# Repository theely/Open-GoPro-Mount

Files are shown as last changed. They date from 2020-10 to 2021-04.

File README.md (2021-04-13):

# Open GoPro Mount

A modular open source GoPro mount for FPV Drones.

## STL Files

[STL files](./STL) are ready to print GoPro Mounts, all available combinations of camera holders and frames mounts are available in the [STL folder](./STL)
If your specific camera model or frame is not yet supported, please [file a request](https://github.com/theely/Open-GoPro-Mount/issues).

### How to 3D Print

#### Filament

- The main body is designed to be printed with TPU (shore A95 or A98).
- The screen protector is best printed with rigid materials such as PLA, Nylon or hard TPU (shore D58)

#### Slicer Settings

- Infil Density: 30%
- Wall Lines: 4
- Top and Bottom Layers: 4
- Support: Yes

#### Slicer Optimal parts orientation




Note: This part can't be printed without support or the overhang will not print properly.

#### Printed Model Reference



## Design Principle

- Designed to be extremely duravble, ultra light and easy to 3D print.
- Modular approach to allow reusability of the component and easy portability to different quad frame designs.







## How to contribute?

The Open-GoPro-Mount is made of 4 components:

- Camera Holder
- Quad Frame Mount
- Lens protection
- Screen protection

### Porting the Open-GoPro-Mount to a new Quad Frame

To port the Open-GoPro-Mount to a new quad frame it's sufficent to design a new Quad Frame Mount.
Either by adapting an existing mount (e.g. Apex Mount (22.5°).step) or by design a new one from scratch.

The angle of the overal mount is defined by the Frame Mount, multiple mount angles can be supported by providing additional Quad Frame Mount featuring a set of angles.

#### Requirements

Each frame mount should include the following joint pice (red part) in order to be compatible with the Camera Holders.



The joint (red part) has the following dimensions:



Its important to respect the distance between the two red pieces:



### Adapting the Open-GoPro-Mount for a new Camera

To support additional cameras a new Cameras it's sufficent to desing a new Camera Holder.
Either by adapting an existing hodler (e.g. GoPro Hero 5/6/7 Holder.step) or by design a new one from scratch.

#### Requirements

Each camera holder should include the following joint holes in order to be compatible with the Quad Frame Mounts.



Distance between the holes are standardised and can not be changes.





The width of the holes does not necesarely be respected as long as there is enought material for the Quad Frame Mounts to join with the Camera Holder.



## Source File (Designs)

### Fusion360 Project

You can access the source design directly from the shared Fusion360

- [Fusion360 project](https://gmail784198.autodesk360.com/g/projects/20201018344143181/data/dXJuOmFkc2sud2lwcHJvZDpmcy5mb2xkZXI6Y28uZjc2MFRFNlhSaW1rVDFkaDE2NXdIdw)

### Step Files

Or you can import the shared step files and edit them in your favorite CAD program.

##### Cameras

- GoPro Hero 5/6/7
  - GoPro Hero 5/6/7 Holder.step
  - GoPro Hero 5/6/7 Holder Large.step (for wide frame mounts)
  - GoPro Hero 5/6/7 Lens Protection.step
  - GoPro Hero 8 Holder.step
  - GoPro Hero 8 Lens Protection.step

##### Frames

- Apex Support (22.5° and 15°).step
- DRC Flow Support (30°).step
- HyperLow 30x30 Mount (30°).step

##### Screen Protection

- GoPro Screen Protection.step

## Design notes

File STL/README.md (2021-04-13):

# STL Files

## How to 3D Print
### Filament
* The main body is designed to be printed with TPU (shore A95 or A98).
* The screen protector is best printed with rigid materials such as PLA, Nylon or hard TPU (shore D58)
### Slicer Settings
* Infil Density: 30%
* Wall Lines: 4
* Top and Bottom Layers: 4
* Support: Yes

### Slicer Optimal Parts Orientation




Note: This part can't be printed without support or the overhang will not print properly.

## Parts

### Screen Protections
* [GoPro Screen Protection.stl](./GoPro%20Screen%20Protection.stl)

### Frames

* Apex
  * [GoPro Hero 5/6/7 15°](./Apex%20-%20ImpulseRC/Apex%2015%C2%B0%20GoPro%20Hero%205-6-7%20Mount.stl)
  * [GoPro Hero 5/6/7 22.5°](./Apex%20-%20ImpulseRC/Apex%2022%C2%B0%20GoPro%20Hero%205:6:7%20Mount.stl)
  * [GoPro Hero 8 22.5°](./Apex%20-%20ImpulseRC/Apex%20GoPro%20Hero%208%20Mount%2022°.stl)
  
* Flow
  * [GoPro Hero 5/6/7 30°](./Flow%20-%20DemonRC/Flow%2030°%20GoPro%20Hero%205-6-7%20Mount.stl)

* Hyperlow
   *  [GoPro Hero 5/6/7 22.5°](./Hyperlow%20Frames/HyperLow%2030°%20GoPro%20Hero%205-6-7%20Mount.stl)
   *  [GoPro Hero 8 22.5°](./Hyperlow%20Frames/HyperLow%2030°%20GoPro%20Hero%208%20Mount.stl)

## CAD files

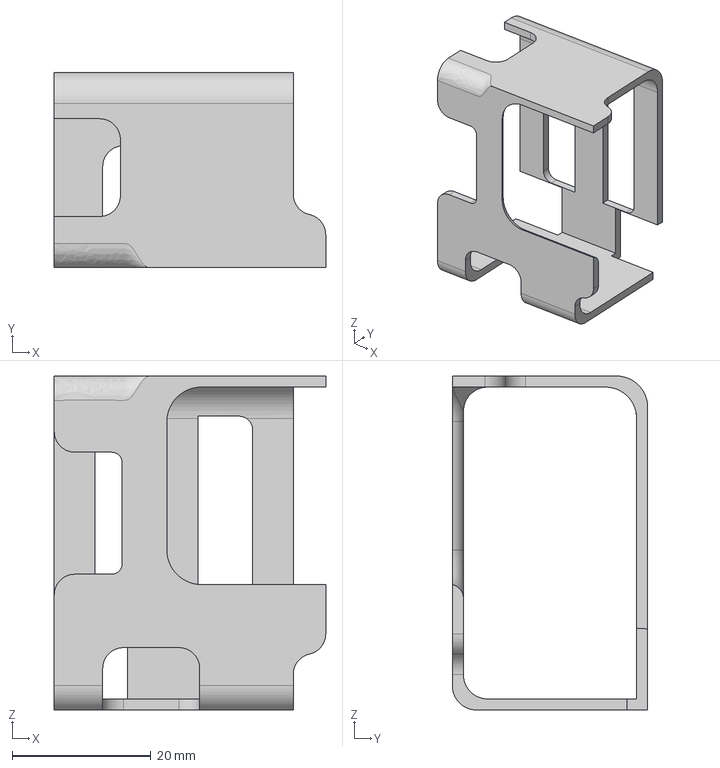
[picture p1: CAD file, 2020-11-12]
STEP/Cameras/GoPro Hero 5-6-7 Holder Large.step
39.2 x 28.2 x 48.2 mm

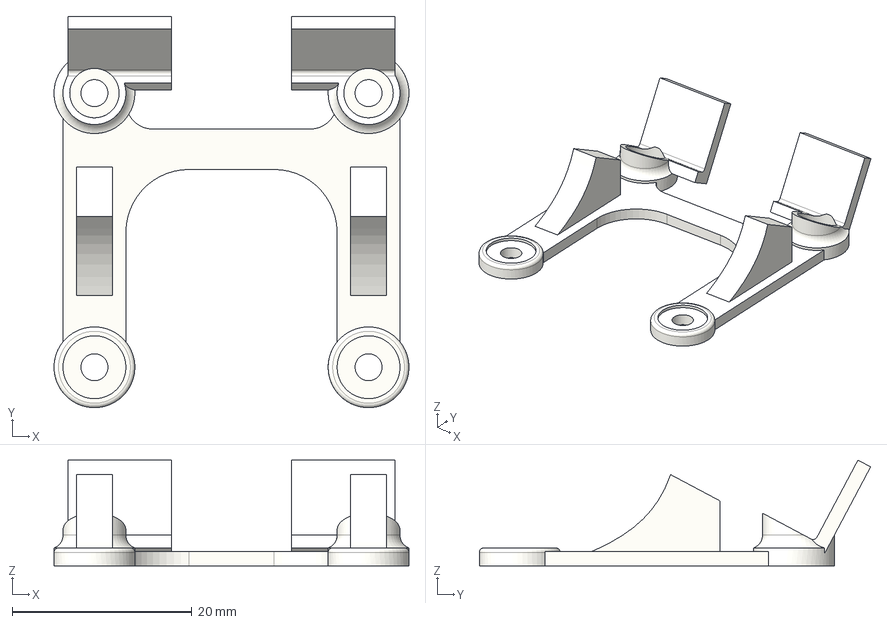
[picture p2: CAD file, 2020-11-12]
STEP/Frames/HyperLow 30x30 Mount (30°).step
39.5 x 43.5 x 11.8 mm

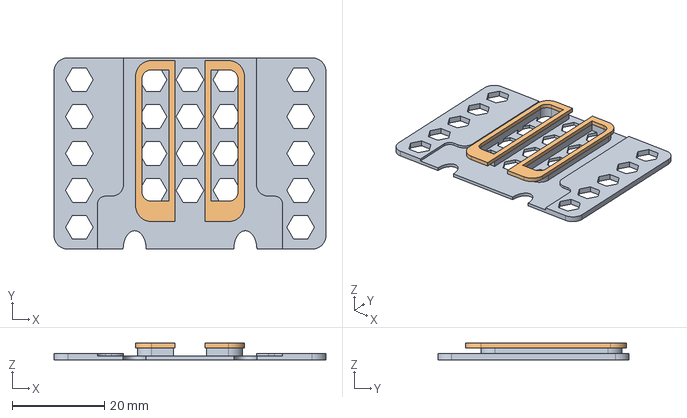
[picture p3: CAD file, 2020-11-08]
STEP/GoPro Screen Protection.step
59.0 x 41.5 x 3.60 mm

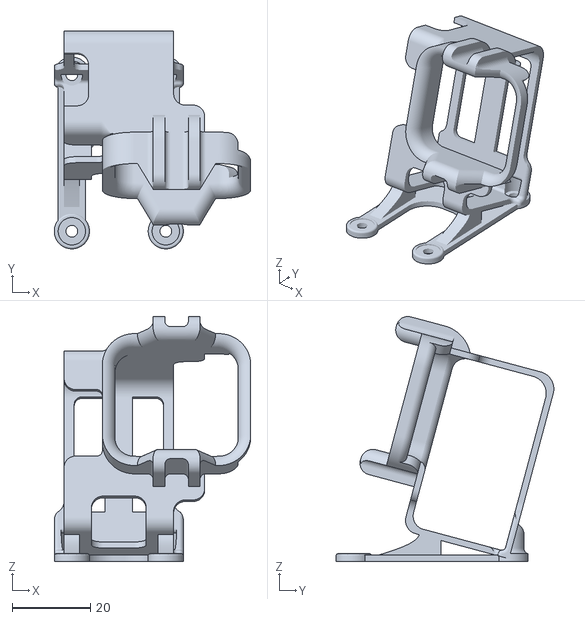
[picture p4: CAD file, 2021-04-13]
STL/Apex - ImpulseRC/Apex 15° GoPro Hero 5-6-7 Mount.stl
50.2 x 55.6 x 62.6

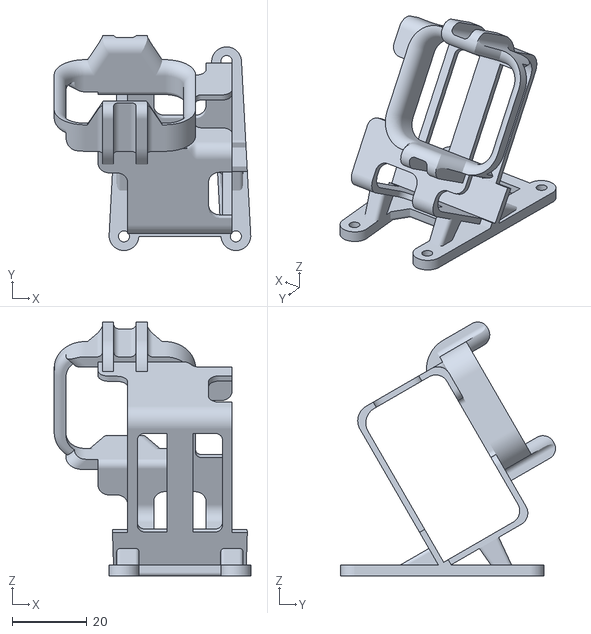
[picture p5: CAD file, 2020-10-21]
STL/Flow - DemonRC/Flow 30° GoPro Hero 5-6-7 Mount.stl
52.7 x 57.6 x 68.1

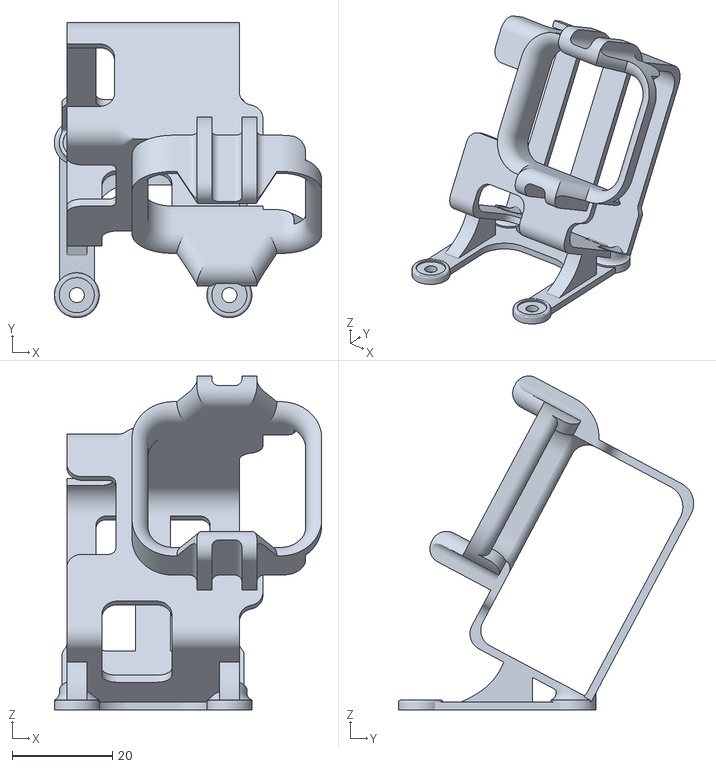
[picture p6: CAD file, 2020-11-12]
STL/Hyperlow Frames/HyperLow 30° GoPro Hero 5-6-7 Mount.stl
53.4 x 59.0 x 66.8

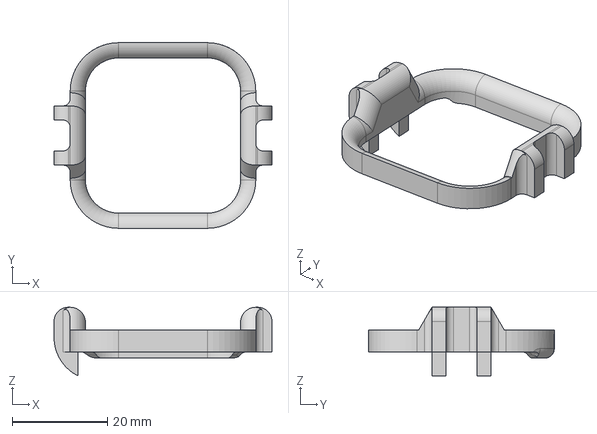
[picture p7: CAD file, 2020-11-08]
STEP/Cameras/GoPro Hero 8 Lens Protection.step
45.8 x 39.0 x 14.4 mm

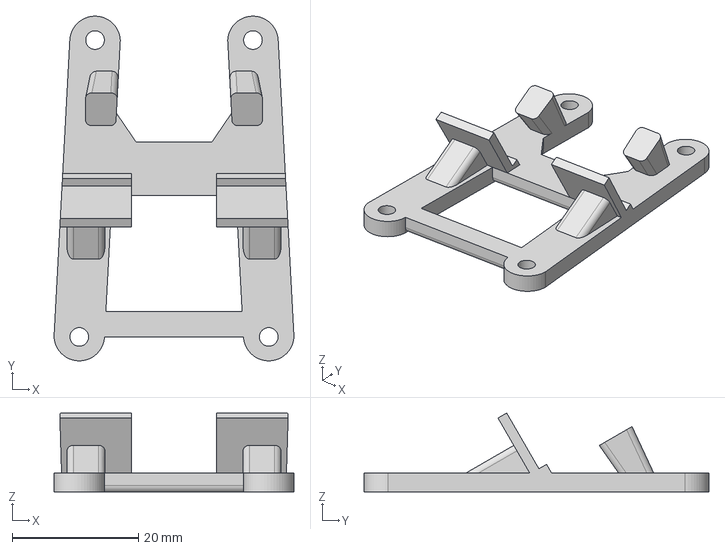
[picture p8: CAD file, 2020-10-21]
STEP/Frames/DRC Flow Mount (30°).step
38.0 x 54.6 x 12.5 mm

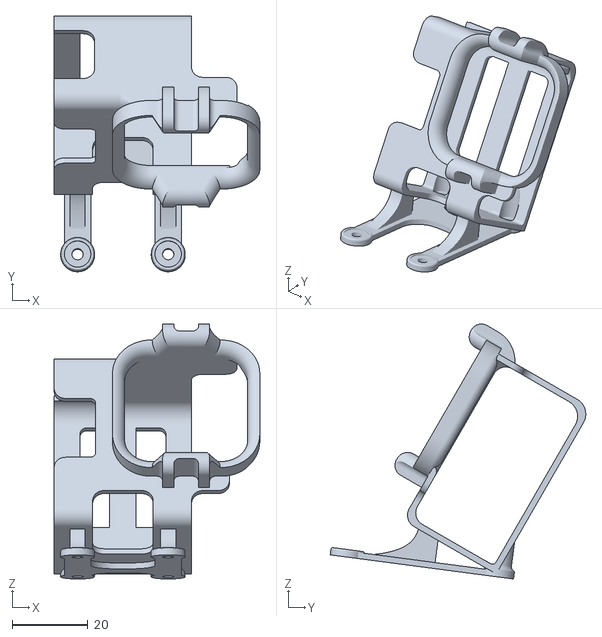
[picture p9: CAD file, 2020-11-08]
STL/Apex - ImpulseRC/Apex GoPro Hero 8 Mount 22°.stl
54.5 x 67.7 x 67.6

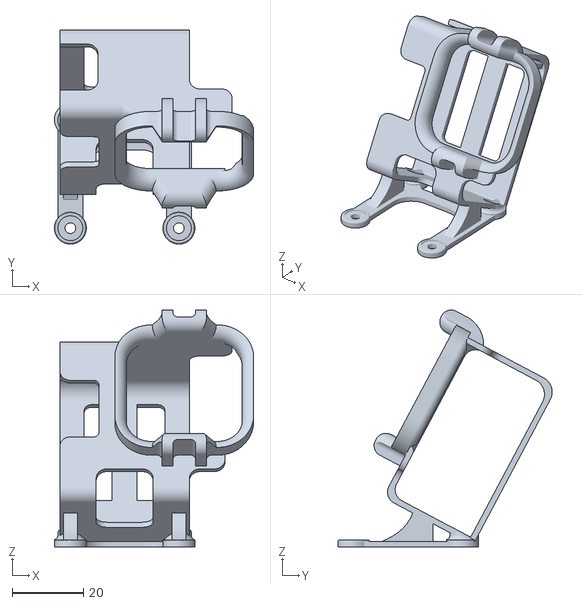
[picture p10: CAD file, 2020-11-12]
STL/Hyperlow Frames/HyperLow 30° GoPro Hero 8 Mount.stl
56.0 x 60.2 x 66.6

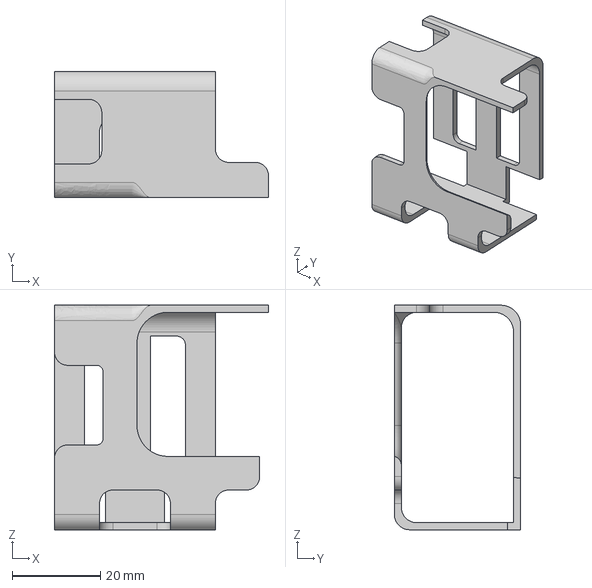
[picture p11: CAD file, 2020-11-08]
STEP/Cameras/GoPro Hero 8 Holder.step
48.4 x 28.6 x 50.8 mm

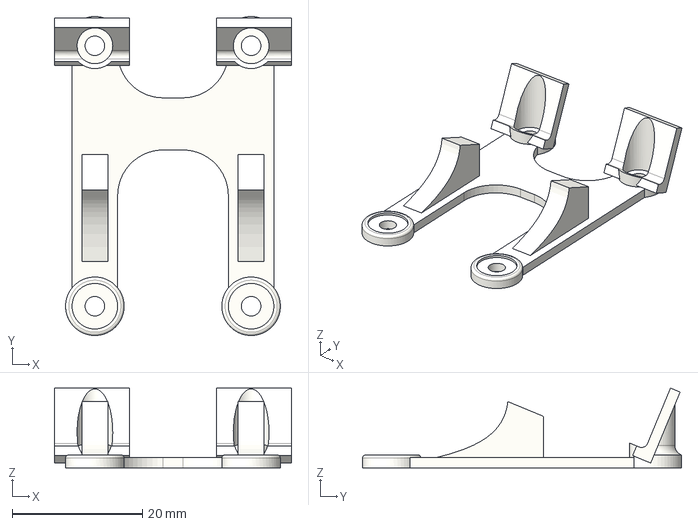
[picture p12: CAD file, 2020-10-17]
STEP/Frames/Apex - ImpulseRC Mount (22.5°).step
36.4 x 49.0 x 12.3 mm

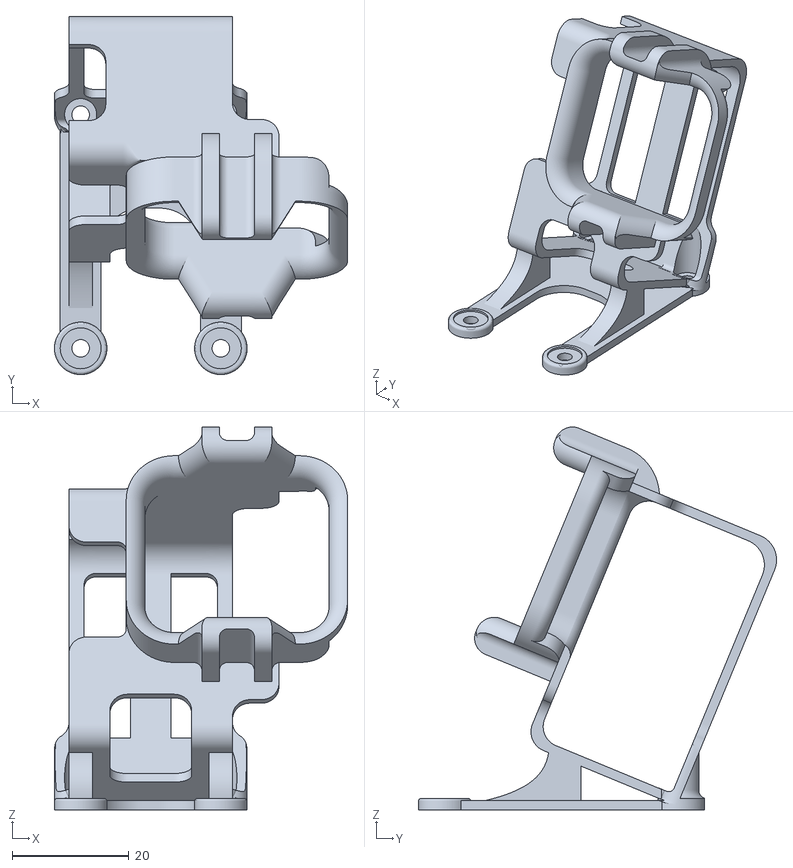
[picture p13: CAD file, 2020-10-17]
STL/Apex - ImpulseRC/Apex 22° GoPro Hero 5:6:7 Mount.stl
50.2 x 61.3 x 65.6

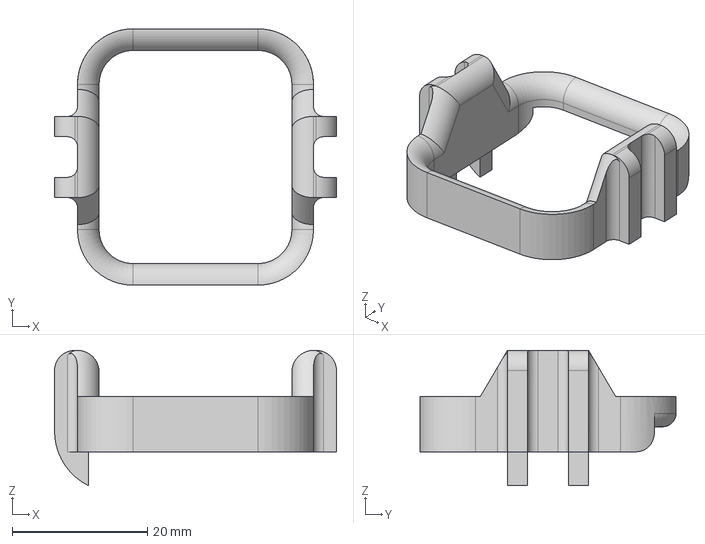
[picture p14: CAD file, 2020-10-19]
STEP/Cameras/GoPro Hero 5:6:7 Lens Protection.step
41.7 x 37.9 x 20.0 mm

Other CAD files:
STEP/Cameras/GoPro Hero 5:6:7 Holder.step
STL/GoPro Screen Protection.stl

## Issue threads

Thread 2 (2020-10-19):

GoPro 8 Black support

dweight, 2020-10-19:
Hi there!
First of all, great initiative, thank you!

I was wondering if there is a possibility to get gp 8 holder and protector?
I'm currently working on a mount for our local frame (DRC Flow) but I'm just a hobbyist and my CAD skills are limited :D
I also assume I can create a PR when my design will be ready? What should be included in it?

theely, 2020-10-20:
Hi,
this is awesome news, GoPro 8 was highly requested!
Yes sending a PR that includes the new STLs and STEPs files would be the preferred way to contribute.

If you need help and guidance to get started we can discuss the design changes in this comment.

I suggest reading the "How to contribute" sections, specifically the part for a new camera holder, it provides a few pointers to get started.
I can also help by trying to adapt the GoPro 5/6/7 holder but I need measurements of the GoPro 8.

p.s. If you are using Fusion360 you can access all designs as reference to create new ones.
p.p.s. in case you want to add support for the DRC Flow feel free to file a separate request, looking at the frame design it just be quite straightforward.

dweight, 2020-10-20:
It would be great if you could adapt adapt the GoPro 5/6/7 holder for GP8, I'm almost finished with the frame adapter :)
I've measured my camera and it is:
Body:
66.60mm wide
48.2mm tall
24.6mm thick
Lens:
32.60mm wide
32.60mm tall
3.81mm thick

I've tried to be as precise as possible, but i feel my calipers are starting to go off a bit so let's say it is accurate to 0.02mm.

theely, 2020-10-20:
Is the lenses aligned on the top right corner of the GoPro or is there any
gap?

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

dweight, 2020-10-20:
It is completly flat with top and right corner

theely, 2020-10-20:
One more thing, I need the front screen measurements (size and position)

dweight, 2020-10-20:
Position:
12mm from the top
8mm from the left corner
Size:
18mm x 18mm

theely, 2020-10-20:
Here is a first prototype of the GoPro Hero 8 Holder.
Could try printing it and suggest adjustments, would be great if you could document by taking photos.
[GoPro Hero 8 Holder v5.stl.zip](https://github.com/theely/Open-GoPro-Mount/files/5410260/GoPro.Hero.8.Holder.v5.stl.zip)

dweight, 2020-10-20:
Sure! Thanks a lot! Will print tonight and let you know tomorrow :)

dweight, 2020-10-21:
Ok, the result is almost perfect, I forgot to measure position of the record button previously (sorry for that!) and it needs to be ~7 mm bigger (look at the button photo).
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
Great work!

theely, 2020-10-21:
Good new!!
Is there a 1mm gap between the camera screen and the back of the mount? We need that in order to install the screen protector. If you want I can send you the STL for the screen protection to test the fit?

dweight, 2020-10-21:
I was about to print the screen protector isn't it universal? Judging by the eye it looks like there is enough space to put protector.
You can send me the screen protector stl :)

Additionally I think it would be a good idea to have some kind of frame around the lens, just enough to protect the lens from being smashed against something unexpected :D

dweight, 2020-10-21:
Ok, I've printed the screen protector and it fits quite nice into your design, but unfortunately when centering it with the camera screen I need to move whole mount ~4mm to the left as shown on the picture below:
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

theely, 2020-10-21:
Alright, I need some additional data.

Screen protection:
- Is it big enough? is the full screen covered especially the corners?
- Could you send me a picture of the back of the GoPro inside the mount with the screen protection on?

Lens protection:
- The holder prototype was without lens protection to help assess the fitting, the final version will include it.
- I'll send you a STL to test the lens protection and one to test both holder + lens protection

Adjustments:

1. move the lens hole 4mm to the right
2. move front screen 4mm to the right and 0.5mm to the bottom
3. increase button hole length by (9mm + 4mm) and shift it 1mm to the back
4. anything else? Maybe could you send (top, front and back) pictures with the screen centred on the screen protection?

dweight, 2020-10-21:
The screen is ~ 58mm x 40mm. Current screen protector covers it but I feel it could be a bit larger (maybe +1 mm in both dimensions).

I positioned camera in the holder as precise as I could and measured the gap between lens and mount again it shows now 3mm (not 4mm as per previous measurement).

Record button is 14.5mm x 14.5mm and its positioned ~10mm from the left edge.

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

theely, 2020-10-21:
I have update the design, and exported the STL for:
- the lens protection only (to test the fitting)
- the holder + lens protection (I suggest you to try this only if the lens protection fits well)

[GoPro 8.zip](https://github.com/theely/Open-GoPro-Mount/files/5418164/GoPro.8.zip)

Regarding the screen protection, If the current one fully covers the screen I would keep it as is. This way we don't have to maintain two different screen protections but we can use the same for all GoPros.

dweight, 2020-10-22:
Hi!
I've printed and fit tested the lens protector. The overall dimensions are ok but bottom and left wall of the lens have a small fillet. It might be a good idea to take it under consideration. Please refer to the pictures:

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

theely, 2020-10-22:
Looks like the radius for the rounded corners needs to be increased.
There's a fillet but it's on the main holder not the lens protection. Could you try this new version?
[GoPro 8.zip](https://github.com/theely/Open-GoPro-Mount/files/5422112/GoPro.8.zip)
> It's better to test the fitting with the camera installed in the main holder.

Could you also turn on the camera in Superview mode and check that the lens protection is not visible in the recording?

dweight, 2020-10-22:
Should I print whole mount or only the lens protector?

theely, 2020-10-22:
I would try the lens protector  first (you can use the old GoPro holder you already printed and add the lens protection on top).
If the lens protector fits well you can test the whole mount.

dweight, 2020-10-23:
Hi, lens protector dimension wise fits ok. You can see the corners of it in super view mode though.
Also the button cut is around 3mm too much.

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

theely, 2020-10-23:
There are a few problems here:

- The GoPro 8 lens is much shorter compared to the 5/6/7. The lens protection "ring" should cover the lens (see attached image) could you provide me measurements for the green sections.
- The GoPro Holder not "thick" enough, the back side is supposed to be flat not curved. Also looks like the screen protection is not installed correctly it should be completely flat against the back wall of the GoPro holder.

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

This is a reference image of the Hero 5/6/7:

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

dweight, 2020-10-23:
The measurements from top to bottom of your picture 2mm, 4mm (from the flat surface of the camera), 2mm. The screen protector is mounted correctly (flat to the gopro), the curving happens due to the screen protector 'horns' which I've removed and it probably wouldn't be a problem when you change the design to resemble 5/6/7 one (back of the mount).

theely, 2020-10-23:
I have reduced the lens protection thickens and adjusted the button hole width.
The screen protection hole are the one compatible with the universal screen protection.

[GoPro 8 - test 3.zip](https://github.com/theely/Open-GoPro-Mount/files/5429305/GoPro.8.-.test.3.zip)

To install the screen protection:
1. Make sure you removed the support under the bottom "horns" overhang.
2. Install it by pushing the bottom overhang into the GoPro holder first and then press the rest in.

dweight, 2020-10-24:
Hi, the latest version fits well, there is no interference with super view and all cutouts are in right dimensions. Really nice job!

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

p.s. I was referring to these as horns:
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

p.p.s. Maybe it is a good idea to make cutouts for these horns in this version also, what do you think?

theely, 2020-10-24:
Not bad! There is still a few places that we could improve.

1. The GoPro holder near the button looks deformed.
2. The bottom of the GoPro holder looks a bit stretched.

What about applying the following changes:

- Increase the GoPro mount height by 0.2mm
- Removing 2mm from both sides of the mount (violet rectangles)

What do you think?

p.s. I have opened a [separate issue](https://github.com/theely/Open-GoPro-Mount/issues/5) to discuss the Screen protection improvements

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

dweight, 2020-10-24:
> * Increase the GoPro mount height by 0.2mm
> * Removing 2mm from both sides of the mount (violet rectangles)
Yep, we can try :)

theely, 2020-10-25:
Let me know what you think, this version is exactly like the one for the Hero 7.
It has just the strictly necessary material to hold the camera and protect the most sensitive parts (lens and screen) with the benefit of being extremely light weight.

[Apex GoPro Hero 8 Mount 22.5° v6.stl.zip](https://github.com/theely/Open-GoPro-Mount/files/5434924/Apex.GoPro.Hero.8.Mount.22.5.v6.stl.zip)

dweight, 2020-10-26:
Great!
I won't be able to print it till next week (I'm away from the printer) so please bear with me :)
Will update the comment with results when ready.

dweight, 2020-11-02:
Hi, a new version of the mount is almost perfect. With the new screen protector in place, there is a bit too much play, same with the vertical fit. I think it would fit better with 1 - 1.5mm smaller dimensions (height and thickness)

theely, 2020-11-03:
Great, here us an updated version:
[Flow GoPro Hero 8 Mount 30° v2.stl.zip](https://github.com/theely/Open-GoPro-Mount/files/5482156/Flow.GoPro.Hero.8.Mount.30.v2.stl.zip)

While setting up the whole mount I have found a small bug in your Flow Quad Frame Mount:
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

Could you double check the measures and verify the meet the requirements listed here:
https://github.com/theely/Open-GoPro-Mount#porting-the-open-gopro-mount-to-a-new-quad-frame

dweight, 2020-11-08:
Ok, I've printed and tested the new version and it fits tight (as expected) :) Thanks for helping with this!
As for the Flow mount, I'll look into it later this week and fix it.

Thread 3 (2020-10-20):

DemonRC Flow

dweight, 2020-10-20:
Hi, I've created a 30deg GoPro Hero 5/6/7 mount for DRC Flow and would like to get access to the repo in order to publish it :)

theely, 2020-10-20:
With pleasure!
Feel free to open a pull request. If you need help just drop a comment here.

dweight, 2020-10-20:
It looks like I need a write access  in order to push my changes and open PR. Would you mind adding me (dweight) to the allowed list?

theely, 2020-10-20:
Pull requests should be open to everyone.
First you need to create a fork of the project, then you make the changes on your fork and only then you should be able to marge your changes with a PR.

Or is there a simpler way?

theely, 2020-10-20:
From GitHub doc: https://docs.github.com/en/free-pro-team@latest/github/collaborating-with-issues-and-pull-requests/creating-a-pull-request

dweight, 2020-10-21:
Thanks for the tip :) I'll try it that way.

Closed 2020-10-21.

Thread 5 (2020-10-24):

Improve Screen Protection fitting

theely, 2020-10-24:
Fitting the screen protection is quite challenging due to the very small tolerances.

Are the lateral supports required or even without them the screen protection is well anchored to the GoPro holder?
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

New simplified version:
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

[GoPro Screen Protection v24.stl.zip](https://github.com/theely/Open-GoPro-Mount/files/5433125/GoPro.Screen.Protection.v24.stl.zip)

dweight, 2020-11-02:
Hi! I've printed and tested the fitting - fits firm into the mount.

theely, 2020-11-08:
Great, going to close this issue! I have updated the STEP and STL files

Closed 2020-11-08.

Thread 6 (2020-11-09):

HyperLow Frame Support

QingwenWei, 2020-11-09:
Support for all hyper low frames just requires a 30x30 mm mounting pattern.

theely, 2020-11-09:
This should be straightforward, I'll add it.

theely, 2020-11-10:
Could you please test this first prototype and let me know if it fits well?
[HyperLow GoPro Hero 8 Mount 22° v4.stl.zip](https://github.com/theely/Open-GoPro-Mount/files/5515495/HyperLow.GoPro.Hero.8.Mount.22.v4.stl.zip)

QingwenWei, 2020-11-10:
I printed just the base to test. There is some misalignment.
Sorry for not really going into detail on the mounting pattern. It's a 30.5 x 30.5 mm pattern like that of a 30x30 flight controller. So a square of 30.5x30.5 m with holes in each corner. The front holes are too narrow and the rest probably should get the extra .5 mm distance to get the prefect fit.

theely, 2020-11-10:
No problem! Could you please send me a photo? It helps to understand how to further improve the mount.

QingwenWei, 2020-11-10:
Yeah sure.
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

theely, 2020-11-10:
Great that was super helpful!
I have fixed a bug on the front mounting holes and extended to 30.5mm.
[HyperLow GoPro Hero 8 Mount 22.5° v5.stl.zip](https://github.com/theely/Open-GoPro-Mount/files/5519899/HyperLow.GoPro.Hero.8.Mount.22.5.v5.stl.zip)

QingwenWei, 2020-11-10:
Fits perfect now, the only thing is the outside of the front mounting holes is slightly biggger then the frame.
Also could you do it for the hero 7 at 30 degrees. Thank you so much for develpoing this!
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

theely, 2020-11-12:
Ready!
In the STL folder you can find a 30° mount for GoPro Hero 7 and 8.

Closed 2020-11-12.

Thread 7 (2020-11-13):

Screen Protector

MuninnFPV, 2020-11-13:
Would recommend making the inserts on the screen protector a little think. Inserts break quite easily.

theely, 2020-11-13:
Thanks for the feedback.
Could you upload a photo of how it broke? Also, what filament did you use? I am getting very solid prints with Nylon.

MuninnFPV, 2020-11-13:
I'm using TPU.
[Uploading IMG_0300 2.pdf…]()

theely, 2020-11-13:
the image was not properly uploaded.

theely, 2020-11-13:
TPU is not ideal for the screen protector because it's not rigid enough.
I suggest you to try with Nylon (best option) or alternatively with PLA or PETG

MuninnFPV, 2020-11-13:
Sorry I meant PLA

theely, 2020-11-13:
PLA should be ok!
Could you please try upload the image again, I can't open it.

theely, 2020-11-16:
Here is a version with larger inserts (2 more layers).  Could you please test it?
[GoPro Screen Protection v27.stl.zip](https://github.com/theely/Open-GoPro-Mount/files/5544679/GoPro.Screen.Protection.v27.stl.zip)

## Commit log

2020-10-17 GoPro Hero 5/6/7 Mount for Apex
    [Apex 22° GoPro Hero 5:6:7 Mount.stl, Universal Screen Protection.stl]
2020-10-17 Added modular step files
    [Apex Support (22.5°).step, GoPro Hero 5:6:7 Mount.step]
2020-10-18 Rename Universal Screen Protection.step to STEP/Universal Screen Protection.step
    [Universal Screen Protection.step]
2020-10-18 Rename Apex Support (22.5°).step to STEP/Apex Support (22.5°).step
    [Apex Support (22.5°).step]
2020-10-18 Rename GoPro Hero 5:6:7 Mount.step to STEP/GoPro Hero 5:6:7 Mount.step
    [GoPro Hero 5:6:7 Mount.step]
2020-10-18 Adding stl folder
2020-10-18 Rename STEP/Apex Support (22.5°).step to STEP/Frames/Apex - ImpulseRC Mount (22.5°).step
    [Apex - ImpulseRC Mount (22.5°).step]
2020-10-18 Rename STEP/GoPro Hero 5:6:7 Mount.step to STEP/Cameras/GoPro Hero 5:6:7 Holder.step
    [GoPro Hero 5:6:7 Holder.step]
2020-10-21 DRC Flow Support
    [Flow - DemonRC (30 deg).step, Flow 30° GoPro Hero 5:6:7 Mount.stl]
2020-10-21 Mount updated with lens protector, naming convention applied
    [DRC Flow Mount (30°).step, Flow 30° GoPro Hero 5-6-7 Mount.stl, Flow 30° GoPro Hero 5:6:7 Mount.stl]
